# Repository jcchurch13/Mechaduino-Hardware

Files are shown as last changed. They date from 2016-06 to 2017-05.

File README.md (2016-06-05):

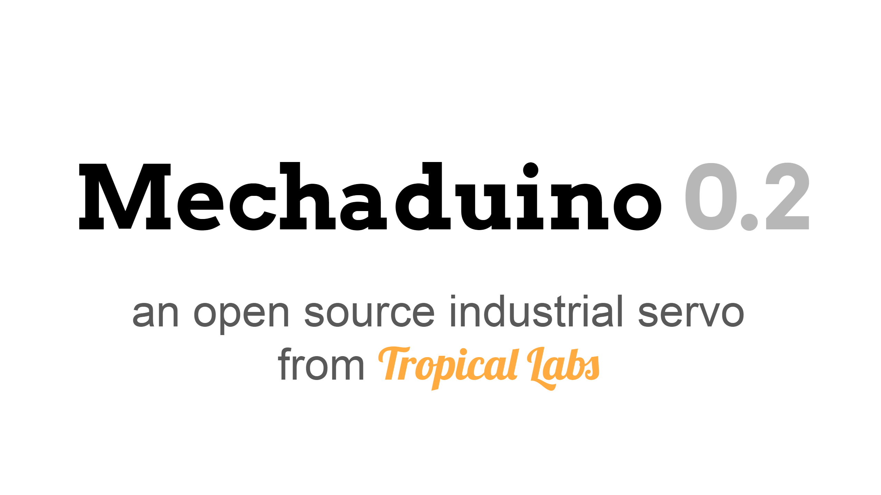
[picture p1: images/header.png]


Engineers use servo motors to achieve the precision motion required in applications such as robotics, automation, and CNC manufacturing. Like RC servos, industrial servos actively correct for external disturbances. Unlike RC servos, industrial servos can provide very accurate motion, and often support advanced motion control modes. Unfortunately the cost of industrial servos is prohibitive to the individual maker (thousands of dollars per motor).

We've been developing an affordable open-source industrial servo motor, opening the door to sophisticated mechatronics applications. Our design leverages the low cost of mass produced stepper motors. We are able to achieve very high resolution via 14b encoder feedback (after calibration routine!).



## Project Goals

 - Position, velocity, torque loops
 - Step & direction inputs for drop-in compatibility with stepper motors / step stick
 - I2c, serial inputs
 - Customizable/open source with access to internal variables
 - Transparent and user-definable control algorithms (commercial servos often lack this)
 - Arduino compatible with easy to use interface
 - High resolution pointing (sub 0.1 degree)
 - Low cost (should not be a huge leap from stepper + stepstick cost)
 - Serial interfaces for inter-motor communication
 - On-board processor allows for stand alone for simple applications
 - Adjustable commutation profiles
 - PID auto tuning
 - Anti-cogging capable
 - Open to customization. Outside of our firmware, we see Mechaduino as a very useful hardware package. If you would like to use the stepper motor in open loop mode w/ encoder to verify location, you can do that.

## Strategy

An industrial servo motor can be broken down into four main components (below). First we looked at each of these components and tried to piece together an affordable breadboard-level prototype. After some experimentation, we were able to distill out a working lineup of components. From there, we've been iterating on our design, working out all the kinks, and tuning the control loops. It's starting to come together!

...Back to those four main components:

1. The actual motor, usually of the brushless dc variety. When you look at industrial servo motors, a big chunk of the cost is the motor itself. They are often custom built, or at least built in limited quantities, which means $$$. Watt for watt, I'd guess that a mass produced NEMA 17 or NEMA 23 stepper motor is between a tenth and a hundredth the cost of the BDC motors used in industrial servos. Although their design is optimized for "stepping," stepper motors are really just 50-pole brushless dc motors. They can be controlled exactly like a more traditional 3 phase BDC motor with more poles. So that's the plan. It's working!

2. A sensor for feedback, usually an encoder. Optical encoders are pretty standard, but get quite pricey if you want high resolution and/or absolute position information. We were intrigued by some of the cheap, high resolution magnetic encoders offered by vendors like AMS. It turns out that although they claim 12 and 14 bit resolutions (that's 0.09 and 0.02 degrees respectively), they suffer from non-linearities on the order of a degree or so! However, we found that this non-linearity is very repeatable, and we were able to develop a quick, self contained (on motor) calibration routine that restores resolution to better than 0.1 degrees. (More on this later. This was a significant design effort and is worthy of its own build log!)

3. Drive circuitry/power electronics to excite the motor windings. Many industrial servos use discrete H bridges. Each phase requires it's own H bridge ( for a two phase motor... half bridges for each in a three phase motor), which consists of at least 4 if not 8 (...including freewheeling diodes) discrete switching devices. Throw in gate drive circuitry, and things start to get expensive. We hoped to find a single-chip, integrated solution that would allow for current feedback, and we found just that in the A4954 dual full bridge PWM driver.

4. Control Electronics. Usually a microcontroller or FPGA. Early on, we decided that Arduino compatibility was a must in order to make the firmware as accessible as possible. We chose to use a SAMD21 ARM M0+ (Arduino Zero compatible) processor to balance cost and performance. Our breadboard prototype system verified that this processor was more than capable of executing the necessary algorithms.

### Application Examples:

 - [Fine, closed loop positioning for 3D printers](https://www.youtube.com/watch?v=T1HIWAiMrfY)
 - Fine pointing for optics (laser, telescope, camera gimbal)
 - Velocity loop for a record player
 - Force feedback/impedance control for robotics
 - Force feedback for gaming controllers
 - Adjustable mechanical impedance: virtual spring,mass,damper
 - Electrical gearing between two axes on a cnc machine, etc.
 - Haptics
 - Tele-operation
 - Gravity-cancellation (counter the gravitational torques on a robotic arm for example)
 - Load detection and characterization (simple case: use as a scale!)
 - Paper towel/tp dispenser
 - Variable load (brake)
 - Variable load (generator)
 - After market valve control (automate a garden hose, etc)

### Other Advantages:

- Finer resolution than stepper motors (0.02 degrees)
- True closed loop for disturbance rejection
- Lower power consumption: only uses power to fight disturbances. This in turn means higher peak torque.
- Absolute position control (not incremental). No need to home on power-on.

## License

All Mechaduino related materials are released under the
[Creative Commons Attribution Share-Alike 4.0 License](https://creativecommons.org/licenses/by-sa/4.0/)

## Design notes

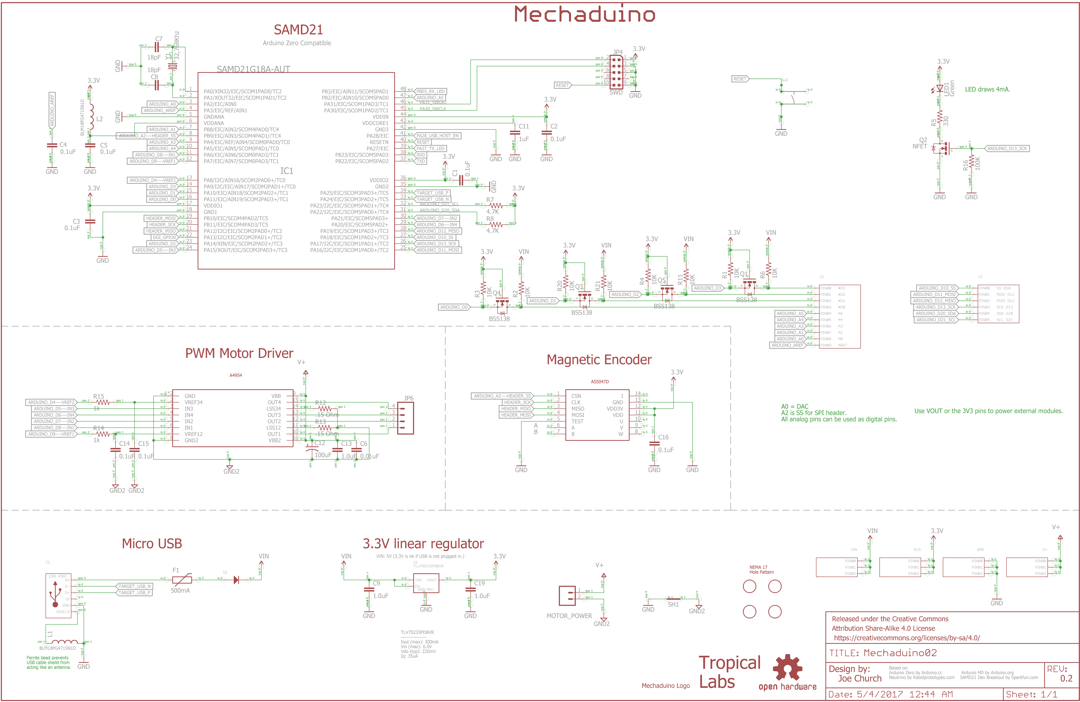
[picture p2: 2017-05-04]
Mechaduino_02_Schematic.png

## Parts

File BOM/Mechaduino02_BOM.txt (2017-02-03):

Partlist exported from C:/Users/jcchurch/Documents/GitHub/Mechaduino-Hardware/Mechaduino02.sch at 2/3/2017 1:24 PM

Qty Value                     Device                                 Package                       Parts                             Description                                                                         
1                             DIODE_SOD-123                          SOD-123                       D1                                Library:  MF_Discrete_Semiconductor                                                 
4                             HEADER_01X03_PTH_2.54MM                PTH_2.54MM_01X03              3V3, GND, V+, VIN                 Library:  MF_Connectors                                                             
1                             HEADER_01X06_PTH_2.54MM                PTH_2.54MM_01X06              J3                                Library:  MF_Connectors                                                             
1                             HEADER_01X10_PTH_2.54MM                PTH_2.54MM_01X10              J2                                Library:  MF_Connectors                                                             
1                             M025MM                                 SCREWTERMINAL-5MM-2           MOTOR_POWER                       Standard 2-pin 0.1" header. Use with                                                
1                             M04PTH                                 1X04                          JP6                               Header 4                                                                            
1                             TACT_4.2MM                             TACT4.2MM                     SW2                               Library:  MF_Switches                                                               
1                             USB_MICRO_RIGHT                        MICROUSB-RIGHT                J1                                Library:  MF_Connectors                                                             
2   .15 Ohm                   R-US_R1206                             R1206                         R12, R13                          RESISTOR, American symbol                                                           
1   0.01uF                    CAP0402                                0402-CAP                      C6                                Capacitor                                                                           
8   0.1uF                     CAP0402                                0402-CAP                      C1, C2, C3, C4, C5, C14, C15, C16 Capacitor                                                                           
2   1.0uF                     CAP0402                                0402-CAP                      C9, C19                           Capacitor                                                                           
1   1.0uF                     CAP0603                                0603-CAP                      C13                               Capacitor                                                                           
1   100K                      R-US_R0402-VISHAY                      R0402-VISHAY                  R16                               RESISTOR, American symbol                                                           
1   100uF                     CAP_POLD                               PANASONIC_D                   C12                               Capacitor Polarized                                                                 
8   10K                       R-US_R0402-VISHAY                      R0402-VISHAY                  R1, R2, R3, R4, R6, R11, R20, R21 RESISTOR, American symbol                                                           
2   18pF                      CAP0402                                0402-CAP                      C7, C8                            Capacitor                                                                           
2   1k                        R-US_R0402-VISHAY                      R0402-VISHAY                  R14, R15                          RESISTOR, American symbol                                                           
1   1uF                       CAP0402                                0402-CAP                      C11                               Capacitor                                                                           
1   32,768Khz                 CRYSTAL2012                            CRYSTAL-SMD-2.0X1.2           Y1                                Various standard crystals. Proven footprints. Spark Fun Electronics SKU : COM-00534 
1   330                       R-US_R0402-VISHAY                      R0402-VISHAY                  R5                                RESISTOR, American symbol                                                           
2   4.7K                      R-US_R0402-VISHAY                      R0402-VISHAY                  R7, R8                            RESISTOR, American symbol                                                           
1   500mA                     PTCSMD                                 PTC-1206                      F1                                Resettable Fuse PTC                                                                 
1   AS5047D                   AS5047D                                TSSOP14                       U$4                                                                                                                   
1   AVAGO_DRIVERTHERM         AVAGO_DRIVERTHERM                      TSSOP16_THERM                 U$1                                                                                                                   
2   BLM18PG471SN1D            INDUCTOR0603-TDK                       0603-TDK                      L1, L2                            Inductors                                                                           
4   BSS138                    MOSFET-NCHANNELSMD                     SOT23-3                       Q1, Q3, Q4, Q5                                                                                                        
1   FRAME-LEDGER              FRAME-LEDGER                           CREATIVE_COMMONS              FRAME1                            Schematic Frame                                                                     
1   Green                     0044_KPT-2012YC                        CHIPLED_0805                  LED1                              LED YELLOW - SMD - 0805                                                             
1   MECHADUINO_LOGO           MECHADUINO_LOGO                        MECHADUINO_LOGO               U$5                                                                                                                   
1   NEMA17_HOLE_PATTERNNEW    NEMA17_HOLE_PATTERNNEW                 NEMA17_HOLE_PATTERN_2         U$2                                                                                                                   
1   NFET                      MOSFET-NCHANNEL2N7002PW                SOT323                        Q2                                Common NMOSFET Parts                                                                
1   OSHW-LOGOMOD              OSHW-LOGOMOD                           OSHW_LOGO_COPPER_MOD          LOGO4                             Open Source Hardware Logo                                                           
1   SAMD21G18A-AUT            INTEGRATEDCIRCUITS_1792_SAMD21G18A-AUT INTEGRATEDCIRCUITS_TQFP48-7X7 IC1                               Atmel D21 32bit ARM Cortex-M0  microcontroller - 48 PIN TQFP                        
1   SHORT-HA5                 SHORT-HA5                              SHORT_ALL-50                  SH1                               Short between two nets                                                              
1   SWD                       CONNETTORI_0171_PH127-205DF055G00A     CONNETTORI_PINHEAD-2X5-P127   JP4                               2x5 PASSO 1,27                                                                      
1   TLV70233PDBVR             TLV70233PDBVR                          SOT-23-5                      U1                                Manufacturer Part #: TLV702                                                         
1   TROPICAL_LABS_LOGO_1LOGO3 TROPICAL_LABS_LOGO_1LOGO3              LOGO3                         U$3

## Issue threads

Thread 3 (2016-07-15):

Vector control

markfinn, 2016-07-15:
From what I can understand of the firmware, and from looking at the schematic, you are missing out on field / vector control of the motor.  With vector control you control the torquing current and the "magnetizing current" (think of the current that is 90 degrees out of phase with the torquing current).  This allows for a few things:

- Easy "current advance" and it's more general cousin "field weakening" which is advance past the point needed for just overcoming inductance.  It allows a much higher top speed when torque is allowed to decline.
- Better position accuracy (and lower position latency) by combining the encoder with the driving currents and a motor model through a Kalman filter.  This especially would help here with the 50 pole motor.
- Some amount of force feedback
- Quieter and cooler operation through sine-drive commutation over square wave. I can't tell exactly what you have implemented now from a quick look at the firmware, so this one might not count.

The reason I bring this up in the hardware project is that you are missing motor feedback that is needed to allow this.  The "normal" way to do vector control is to control the phase drive voltages (via PWM) and sense the phase currents.  To do that you would need to add an amplifier to bias and scale the current sense resistors, and ADCs (maybe in the MCU already? I didn't look) that can sample at least around 40 per pole, or 2000 times per rotation on a 1.8 degree stepper.

Another option that may be possible (I'm making this one up as I go along, I don't know if it's been done before or disproven)... Since you are using a bridge driver that self-regulates current, I think it might be possible to implement vector control using a "control the current, read the phase voltage via PWM transitions" model.  This would depend on being able to change the current Vref values at at least a few times per pole to control the phase current directly, and having some digital feedback from the motor phase outputs to know when the A4954 switches between internal PWM modes.  This method would only need a diode or two and some resistors for each of the 4 motor leads.  The big sticking point would be whether the A4954 Vref input has that kind of frequency response.  I don't see anything to give a hint in the datasheet, so it might have to be determined by experiment.

Either of these methods would allow estimating the back-emf of the motor, which gives an estimate of motor position, and when combined with knowing the phase voltage or current give force feedback and the ability to directly control the 2 current vectors occurring in the motor.

Looking forward to getting some hardware...  I'm glad someone is finally doing this!

jcchurch13, 2016-07-15:
Hi Mark,
We actually are using a form of vector control.  We sinousoidally vary the vref inputs to the a4954 driver as you describe.  Frequency response does not seem to be an issue based on performance.
-Joe

markfinn, 2016-07-15:
I went through the code enough to understand it now. I should have been more specific about using "vector" vs "field oriented" above.  It's been a while since I've looked at this stuff and I got a little sloppy.

What you're doing is vector based, but you're not really getting field control yet because even though you try to command Iq (torque current) via output() and implicitly command Id to zero, the external controller (The PWM current control loop in the A4954) can't magically make those currents happen in the face of inductance and motor irregularity.  The real Iq ends up lagged and not matching the commanded one, and the real Id ends up nonzero.

I see you've tried "phase advance."  Was that by using a motor model (backemf, resistance, inductance, position) to try to estimate the the actual phase currents and Iq, Id?   If that works well enough, maybe my request for real feedback isn't needed.  I just haven't seen any examples where current sensing was modeled instead of measured before so I assumed it didn't work well.

Sorry if you've thought about all this already, I'm a little excited about the project.  For the record, my looking into this part came from seeing the FAQ about motor speed only being easy up to 300rpm on the nema17, combined with the link you posted to the 1.8A nema 23 stepper.  It has an inductance of 17mH, so I started getting a bit worried about top speed even at 40 volts.

jcchurch13, 2016-07-16:
Hi Mark,

You are correct:  We are using vector control, but not field oriented control.  There are a lot of advantages that come with field oriented control, but we've found that it would drive the hardware cost and complexity up quite a lot.  By off-loading the current loop to the A4954, we've found that we can deliver pretty impressive performance at an accessible hardware cost.
Thanks for your input!
-Joe

markfinn, 2016-07-16:
I'm not saying don't use the A4954, I'm saying sense the current.  You
could maybe do it well enough with just AC coupling the shunt into the ADC
channels on the MCU.  That would only be 2 extra caps and 4 resistors.

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

dzid26, 2020-07-23:
I am just going to link to a discussion where I am coming to the same realization as @markfinn regarding a lack of current sensing and FOC implications.
https://groups.google.com/g/smart-stepper/c/LuQkAaiCvPs/m/Nzos9Bh_CAAJ

I am too wondering if it would work to implement a modified (even simpler) open-loop FOC where currents are not sensed but assumed to be correct based on the commanded currents.
I am thinking that without reading or estimating the real current the method wouldn't be perfect but perhaps a little improvement could be noticeable. At very least the math for field weakening, etc could be reused instead of guessing offsets between phases to weaken the field.
Additionally, it seems sensor latency is already a limiting factor for higher speed, so it would need to be accounted for separately via phase-advancement trick.

Closed 2016-08-22.

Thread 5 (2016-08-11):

Current BOM lists 10uF 0402, board uses 10uF 0805 for C18, C10

thantik, 2016-08-11:
Found this mistake while reflowing my boards; caused me to get a digikey order slightly wrong.

jcchurch13, 2016-08-11:
Fixed, thanks!

Closed 2016-08-11.

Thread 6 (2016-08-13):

BOM mismatch between Value and Device - IC2 3.3V regulator - line 31

bitbangr, 2016-08-13:
BOM Line 31 shows 3.3V regulator AP2112K-3.3 as the value however the specified device is AP2202-ADJ.

The AP2202-ADJ needs additional circuitry on pin 4 to set the correct output voltage.

Perhaps update the BOM to reflect the correct device?

1   AP2112K-3.3               AP2202-ADJ                             SOT23-5@1                     IC2

jcchurch13, 2016-08-14:
Fixed, thank you!
-Joe

Closed 2016-08-14.

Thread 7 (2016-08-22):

R6, should this be a 10k?

thantik, 2016-08-22:
There are multiple places that I'm seeing a 10k pullup on the RESET line:

https://cdn.sparkfun.com/datasheets/Dev/Arduino/Boards/sparkfun-samd21-mini-breakout-v10.pdf

http://www.atmel.com/Images/Atmel-42181-SAM-D21_Datasheet.pdf -- Page 1022 under 39.4. External Reset Circuit

But on the schematic and board, R6 is listed as a 330ohm.  This is a pretty strong pullup, is there a reason for the deviation?

jcchurch13, 2016-08-22:
Hi!  R6 is used as a current limiting resistor here (similar to the second resistor in the 39.4 example above).  R1 acts as the pullup (100k).

Closed 2016-08-22.

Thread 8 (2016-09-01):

AS5047D Magnetic Encoder Power Management issue.

bitbangr, 2016-09-01:
I was checking over the [Datasheet for the AS5047D Magnetic Rotary Position Encoder](http%3A%2F%2Fams.com%2Feng%2Fcontent%2Fdownload%2F595083%2F1609657%2F320155&sa=D&sntz=1&usg=AFQjCNHJLUOwhbDV-abh1qcGxdTLYPkByQ)

The section on power management has two configurations. One for 5V operation and the other for 3.3V operation.

For 3.3V operation it states -> "In 3.3V operation, VDD and VREG must be tied together."

In Figure 10 the "3.3 Operation" diagram shows VDD and VDD3V3 tied together with one 100nF cap to ground.

It would seem to me that C17 1uF should be removed from this circuit and pins 11 and 12 of the AS5047D should be tied together.

This could easily be fixed on the current board by a small bridge between C16 and C17 on the top of the board after removing C17.

PS I also [reported this to the Mechaduino Google Group](https://groups.google.com/forum/#!topic/mechaduino/e2BsRLsDtlw)

jcchurch13, 2016-09-01:
We are aware of this discrepancy but have found that it does not seem to have any noticeable effect on performance.  We will make the change in the next rev.
Thanks!
-Joe

bitbangr, 2016-09-01:
Cool.  I'll close this then.

Closed 2016-09-01.

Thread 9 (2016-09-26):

Opensource.com article

spotrh, 2016-09-26:
Joe,

Apologies for opening a github issue, but I couldn't find an email address for you. I'm writing an article for opensource.com on some of the best open source hardware innovations in 3d printing in 2016, and I want to feature the Mechaduino. Would you be able to point me to a picture of the Mechaduino (maybe the "banana" picture from the kickstarter page) that I could use under a Creative Commons license (CC-BY-SA would be ideal)?

Thanks in advance,

Tom Callaway <tcallawa@redhat.com>

jcchurch13, 2016-09-26:
Feel free to use any of the photos on our hackaday.io page:

https://hackaday.io/project/11224-mechaduino

All Mechaduino related materials are released under the Creative Commons Attribution Share-Alike 4.0 License!

Closed 2016-09-26.

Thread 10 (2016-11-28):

Feature request : Gadgeteer port

arthurwolf, 2016-11-28:
Hey.

As part of the Smoothieboard v2 hardware design, we are planning a very complete series of "extension boards" : goo.gl/XP5iZc
Those boards will all use the "Gadgeteer" socket. It is small, it's a very nice and well designed standards, a lot of boars already exist for it. We also hope to encourage other Open-Source controller board designers ( running Smoothie or otherwise ) to also use these in their hardware.
If you were to add a Gadgeteer port to your board, that'd make it super easy to interface will all of the Smoothieboard v2 hardware boards ( and possibly other boards in the future ).
What do you think ? Maybe for a v2 of your hardware ...

Cheers.

npgoalkeeper, 2018-07-26:
RIP Smoothieboard

arthurwolf, 2018-07-26:
What ? Why ?

On Thu, Jul 26, 2018 at 2:46 AM npgoalkeeper <notifications@github.com>
wrote:

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

--
Courage et bonne humeur.

DirtyEngineer, 2018-07-26:
Because development seems to have come to a full stand still?

I think this comment stems from this thread. https://github.com/jcchurch13/Mechaduino-Hardware/issues/14#issuecomment-407940180

arthurwolf, 2018-07-26:
Eh thanks, answered there. This is most definitely wrong.

On Thu, Jul 26, 2018 at 2:51 PM Jon Raymond <notifications@github.com>
wrote:

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

--
Courage et bonne humeur.

npgoalkeeper, 2018-07-26:
Yea I thought it was dead as the website said the release would be in 2017, and the files haven't been updated in awhile. I like the the thing you're developing with F360 and smoothieware, though.

arthurwolf, 2018-07-27:
It's late, but that's to be expected for such a huge project :)

On Thu, Jul 26, 2018 at 11:51 PM npgoalkeeper <notifications@github.com>
wrote:

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

--
Courage et bonne humeur.

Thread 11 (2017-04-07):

Compilation error w/ Arduino 1.8.2 IDE

eudoxos, 2017-04-07:
After opening the firmware in Arduino, verification fails with error from gcc. I tried to google things up, nothing shows up. Maybe some problem between keyboard and chair. I am new to mechaduino so maybe I am missing something obvious. I looks as if types were not recognized, but there is no error about #include not being found. These are the first few messages. Thanks for help!

```
sketch/analogFastWrite.c: In function 'syncADC':
analogFastWrite.c:17: error: invalid type argument of '->' (have 'uint16_t')
   while (ADC->STATUS.bit.SYNCBUSY == 1)
             ^
sketch/analogFastWrite.c: In function 'syncDAC':
analogFastWrite.c:24: error: 'DAC' undeclared (first use in this function)
   while (DAC->STATUS.bit.SYNCBUSY == 1)
          ^
sketch/analogFastWrite.c:24:10: note: each undeclared identifier is reported only once for each function it appears in
sketch/analogFastWrite.c: At top level:
analogFastWrite.c:29: error: unknown type name 'Tc'
 static __inline__ void syncTC_8(Tc* TCx) __attribute__((always_inline, unused));
                                 ^
analogFastWrite.c:30: error: unknown type name 'Tc'
 static void syncTC_8(Tc* TCx) {
```

mikbeng, 2017-10-11:
I have the same problem here, did you find any solution to this?

jcchurch13, 2017-10-11:
I would double check that you have the correct board selected in the Arduino IDE (Arduino/Genuino Zero, (Native USB port)).  I've seen similar issues when I've forgotten to select the right board.

-Joe

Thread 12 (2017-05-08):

NEMA 34 and larger?

linuxras, 2017-05-08:
What would be required to make this work with larger stepper motors like NEMA 34 etc.?

tknapstad, 2017-05-09:
Mainly a beefier motor driver which will probably alter both the schematic and layout, as well as an adapter plate for the nema34 footprint

npgoalkeeper, 2018-08-23:
Just a bracket. Theres a high power version of this for nema 34's.

DirtyEngineer, 2018-08-23:
I might mention there's a Kickstarter for a similar product right now. https://www.kickstarter.com/projects/301805155/ustepper-s-line

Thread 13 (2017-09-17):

Flyback diodes

Blaster1920, 2017-09-17:
Hi,
Why don't you add these diodes [https://github.com/watterott/SilentStepStick/blob/master/hardware/StepStick-Protector_v11.jpg](url) directly on your board? I think it would help a lot the printing quality.

npgoalkeeper, 2018-07-24:
Like in a TL-Smoother Configuration?

Blaster1920, 2018-07-24:
Yes.

npgoalkeeper, 2018-07-24:
Why not just solder one between the stepper and the mechaduino motor.

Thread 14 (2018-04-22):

Feature request: Trinamic drivers

udidnazime, 2018-04-22:
Any word of advice on interfacing trinamic drivers on board instead of the a4954 stepper drivers? This so stepper operation can be quieter.

julidau, 2018-07-23:
could you elaborate further on that thought? Are there any trinamic products specifically that you could suggest ?

npgoalkeeper, 2018-07-24:
I really like the look of the TMC4362A-LA, and they also happen to be cheaper at Digi-key than the TMC4330A-LA, and its information can be found here: https://www.trinamic.com/products/integrated-circuits/details/tmc4361a-la/ as well as the pinout.

julidau, 2018-07-24:
These are nice motion controllers.

They can talk to the AMS5047 directly and implement closed loop stepper control using the encoder feedback.

**But** they do not contain a driver stage or a stepper driver (current controller). So while they are a nice replacement for the M0+ core (the Atmel SAMD21) on the Mechaduino, they cannot replace the A4954.

I feel that i should also mention the [PanDrive stepper controllers from Trinamic](https://www.digikey.de/product-detail/de/trinamic-motion-control-gmbh/PD42-2-1140-TMCL/1460-1100-ND/5013387) that are using a similar chip to implement something close to the Mechaduino. While the linked one is quite pricey i think they are a better option then changing the mechaduino hardware.

npgoalkeeper, 2018-07-24:
Would it be possible to use that with the tmc 262 as the stepper driver? or would that drive the price of this device to be over a hundred dollars (im trying to add this to my prusa i3 mks MMU kit. I’ve looked at Trinamic’s PANdrive systems and am not interested to to the insane price).

npgoalkeeper, 2018-07-24:
In that case, what about using a TMC5160-TA? I wasn’t able to find it beforehand on the other comment, however it includes the features of the TMC2660 with an input for an encoder, along with the features of the TMC4362A-LA. along with that, it is chainable via UART on the datasheet. Along with that, you can add extrernal mosfets, making this closed loop stepper sytem seem more attractive to cnc applications. e. g. one large stepper board chained to multiple smaller, cheaper ones. This IC is also cheapper than the TMC262 and TMC4362-LA at digikey.

julidau, 2018-07-25:
well that chip sure looks great. I really wish i would have known about it before making a driver based on the TMC2660 :)

That chip only has a few drawback though:
- The Encoder interface accepts quadrature encoders only. It makes sense (most stepper motors come with quadrature encoders either build in or added) but is different from the TMC4362-LA, which also accepts absolute position encoder feedback. Not that one would need that anyway, quadrature should be fine for most applications. A replacement for the AMS5047 would be the [AMS5601](https://www.digikey.com/short/j5v2mn) with a quadrature interface.
- The external mosfets are not optional, they are required. The chip only contains mosfet drivers. This is not that big of a deal as low power mosfets can be had for a buck each, but one will need 8 of them.

I am quite confident that, using the TMC5160-TA, a drop-in replacement for the mechaduino can be made. I'm not sure about doing it on two layers, but it might be possible. I unfortunately lack the time to do so :(

npgoalkeeper, 2018-07-25:
Huh. So to get a better, cheaper motion controller/ driver, you have to sacrifice some precision? Not like over 10 thousand positions would affect something that only steps to 400. When will the TMC 2660 variant of this driver be available? Will it still maintain the SAMD21G18A-AUT? No Rush.

julidau, 2018-07-25:
just in case it seemed that way: i am not affiliated with the mechaduino project :wink:.  I just happen to own one...

As it seems this project died over a year ago, i don't think there will be any version using a trinamic driver. I was working on a different driver style using the TMC2660 (one in a format similar to [this one](https://www.aliexpress.com/item/Dawupine-Schrittmotorsteuerung-Leadshine-DM856-2-phasen-schrittmotor-57-86-Digitale-Schrittmotortreiber-20-80-Vdc-1A-bis/32835988065.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,searchweb201603_46,ppcSwitch_2&algo_expid=c5cd6080-6b93-4cec-9fca-baf0c47b8db8-6&algo_pvid=c5cd6080-6b93-4cec-9fca-baf0c47b8db8&priceBeautifyAB=0)).

Regarding the encoder and the loss of precision: The AMS5047 is currently hard to come by (mouser has a few left i think) and the one i proposed was the "next best thing". Whether that would be the optimal choice i cannot say for certain. AMS might have 14bit encoders with a quadrature interface in their lineup. I was not looking super hard to be honest…

Cheers :)

npgoalkeeper, 2018-07-26:
Wow. Now I feel stupid. So um, thanks for your help. It seemed like you were putting an awful lot of effort into your replies, and I thank you for that. It seems that a lot of things 3D-Printing as far as electronics go have died in the past year. The Smoothie-V2 seems to be dead, as well as many other awesome boards. With duet being at the, top they really have no reason to innovate and the revolve board will be way too expensive for a standard user. This makes me curious of someones gonna end up making a REALLY successful kick-starter that includes 3D printing electronics. Anyways, thanks again, and one last thing: Are you gonna make that motor driver design public on easyEDA? I think they guys over at reprap would have a field day over that.

julidau, 2018-07-26:
No worries! I just wanted to lower the expectations a bit :)

Yes, i was planning on making the design publicly available after fully testing it out. And who knows? Maybe i will come around to making a driver board thats screws to the back of the stepper like mechaduino does. I too am curious what the future holds...

npgoalkeeper, 2018-07-26:
I just did some reading and found out that the TMC5130 has the same features as the 5160, however it has internal MOSFETS, so you may want to check that out at a later date.

arthurwolf, 2018-07-26:
@npgoalkeeper  Smoothie v2 is most definitely not dead, both Smoothie v1 and v2 are very actively developed, it's just we are doing extremely ambitious things at the moment so there are longer development time spans than usual.  I've just sent the gerber for the first proto of v2 to the board house, and we already have protos for v2-mini and v2-pro. And v2 firmware can laser cut and cnc mill at this point.

npgoalkeeper, 2018-07-26:
Sooo its just issues with FW and getting the pcb's manufactured at this point?

arthurwolf, 2018-07-27:
Mostly yes.

On Thu, Jul 26, 2018 at 11:53 PM npgoalkeeper <notifications@github.com>
wrote:

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

--
Courage et bonne humeur.

npgoalkeeper, 2018-07-28:
So I found the AMS AS5311 magnetic hall effect IC, and it uses an ABI interface (looks like it can be programmed to ABN for the TMC5130) and all it requires is an SDI/SCL interface to program. I’m going to try and make something close the mechaduino, and it should in theory only need a location to get to.

julidau, 2018-08-22:
hey,
how is your project coming along ?
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
npgoalkeeper, 2018-09-07:
"Integrated Drive" IC's have too low of an amperage rating for CNC applications. On second thought, I will copy the TMC5160 reference design. Updates on the project will be posted here: https://github.com/npgoalkeeper/Closed-loop-stepper/blob/master/README.md
(I really need a name for it)

npgoalkeeper, 2018-09-14:
Just a bit of an update, I've been talking with trinamic and they have convinced me to simply use a tmc2130, with it the tmc2160 coming out soon.

npgoalkeeper, 2018-09-15:
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
Its begun.

npgoalkeeper, 2018-09-17:
So I did a small amount of research on the VHF ringingyou spoke of, and found a thing called a snubber network. Are therea any downsides to using an RCD snubber? It seems to do the same exact thing as the resistor, however it acts as more "active" filter that completely removes the inductance that causes this phenomenon. However, it seems like more than anything my main concern should be layout as far as efficiency goes when I make the tmc2160 version.

RGD2, 2018-09-18:
Yes, Snubber with diode is better - just more complex, more expensive, and
needs to be the right one.

 But yes, even just one resistor is acting as a snubber, just a simple
linear one.

Diode is non-linear, but so are ceramic caps not of np0 or c0g types — x7r
or any code other than the first two have capacitance which changes (quite
a lot!) with voltage — bad if you want a filter to stay tuned, but the
nonlinearity is actually good for avoiding resonance —   It is impossible
without that linearity. The whole point of a snubber is to prevent
unintended resonance and Q factor from causing a destructive over-voltage
condition.

The simple gate resistor is just enough to drop the Q of the RLC resonator
that exists because there is too little R in the gate pin, and the gate pin
+ pcb trace has some small inductance.

Then you can get into active circuits with transistors set to help turn off
the transistor faster by providing a lower impedance route to ground right
next to the main mosfet gate. All this becomes increasingly important as
you get up to the higher power levels / voltages and currents, since the
energy  in the ringing is a proportion of the gate drive power, and bigger
transistors mean much large gate capacitance, and require higher gate drive
current, and more careful handling of the snubbing.

On Mon, 17 Sep 2018 at 1:45 pm, npgoalkeeper <notifications@github.com>
wrote:

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
--
-- Remy

amoose136, 2018-09-22:
Just a note on the TMC2130-LA: my printer uses an Einsy Rambo 1.1a board as the driver and even though the RMS current is rated for 1.2A, in practice if you print with Marlin setting current at 800mA, the motors will reach a steady state temp around 50C. More current does not seem like a good thing here but I could see that maybe a longer Nema 17 could handle more and use more in milling applications with no issues.

npgoalkeeper, 2018-09-22:
Well I mean, this is mainly just for experinentation. Might be fun to use nema 17's in a milling machine just for wood or MDF or whatever.

npgoalkeeper, 2018-12-09:
So here's me a couple weeks later, after some testing. A friend and I have done some research and written the software, so we are going to make a motion controller that consists of A STM32F401 MCU paired with 2x TMC4361a's and 2x TMC2160's paired with 12a MOSFETs. As of right now, I do not want to share the link to access the project on EasyEDA

Psylenceo, 2019-04-19:
I keep screwing this up. Here is 2 boards I made up to allow more user functionality, use a TMC5130 or TMC2130, and eitehr a atmega32u4 or a atmega328PB. With a 3rd board in progress to offload the driver ic and instead have the user use a break out borad like the TMC2130-BOB, TMC5130-BOB, or TMC5160-BOB.

32u4 board - https://easyeda.com/kenm/Intele-step
328PB board - https://easyeda.com/kenm/mechaduino-328pb

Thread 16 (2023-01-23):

hardware serial rather than USB

jakobbak, 2023-01-23:
Hello All

Apologies for asking a question that may seem trivial, but I haven't been able to find an answer here or in the forks I was able to examine.

I was hoping to be able to use the serial interface, but over normal serial pins rather than USB. Are any of the existing pins available on the board attached to a serial peripheral? I realise I'll probably have to write up the serial handling myself, and happy to give that a shot, but in case there is another project that has done the same I'd be happy to take a pointer to such a project :)

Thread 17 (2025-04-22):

Missing Drill files

schnibbi, 2025-04-22:
For Ordering the PCBs at JLCPCP there is an issue with missing drill files.
Can you porovide the files ?

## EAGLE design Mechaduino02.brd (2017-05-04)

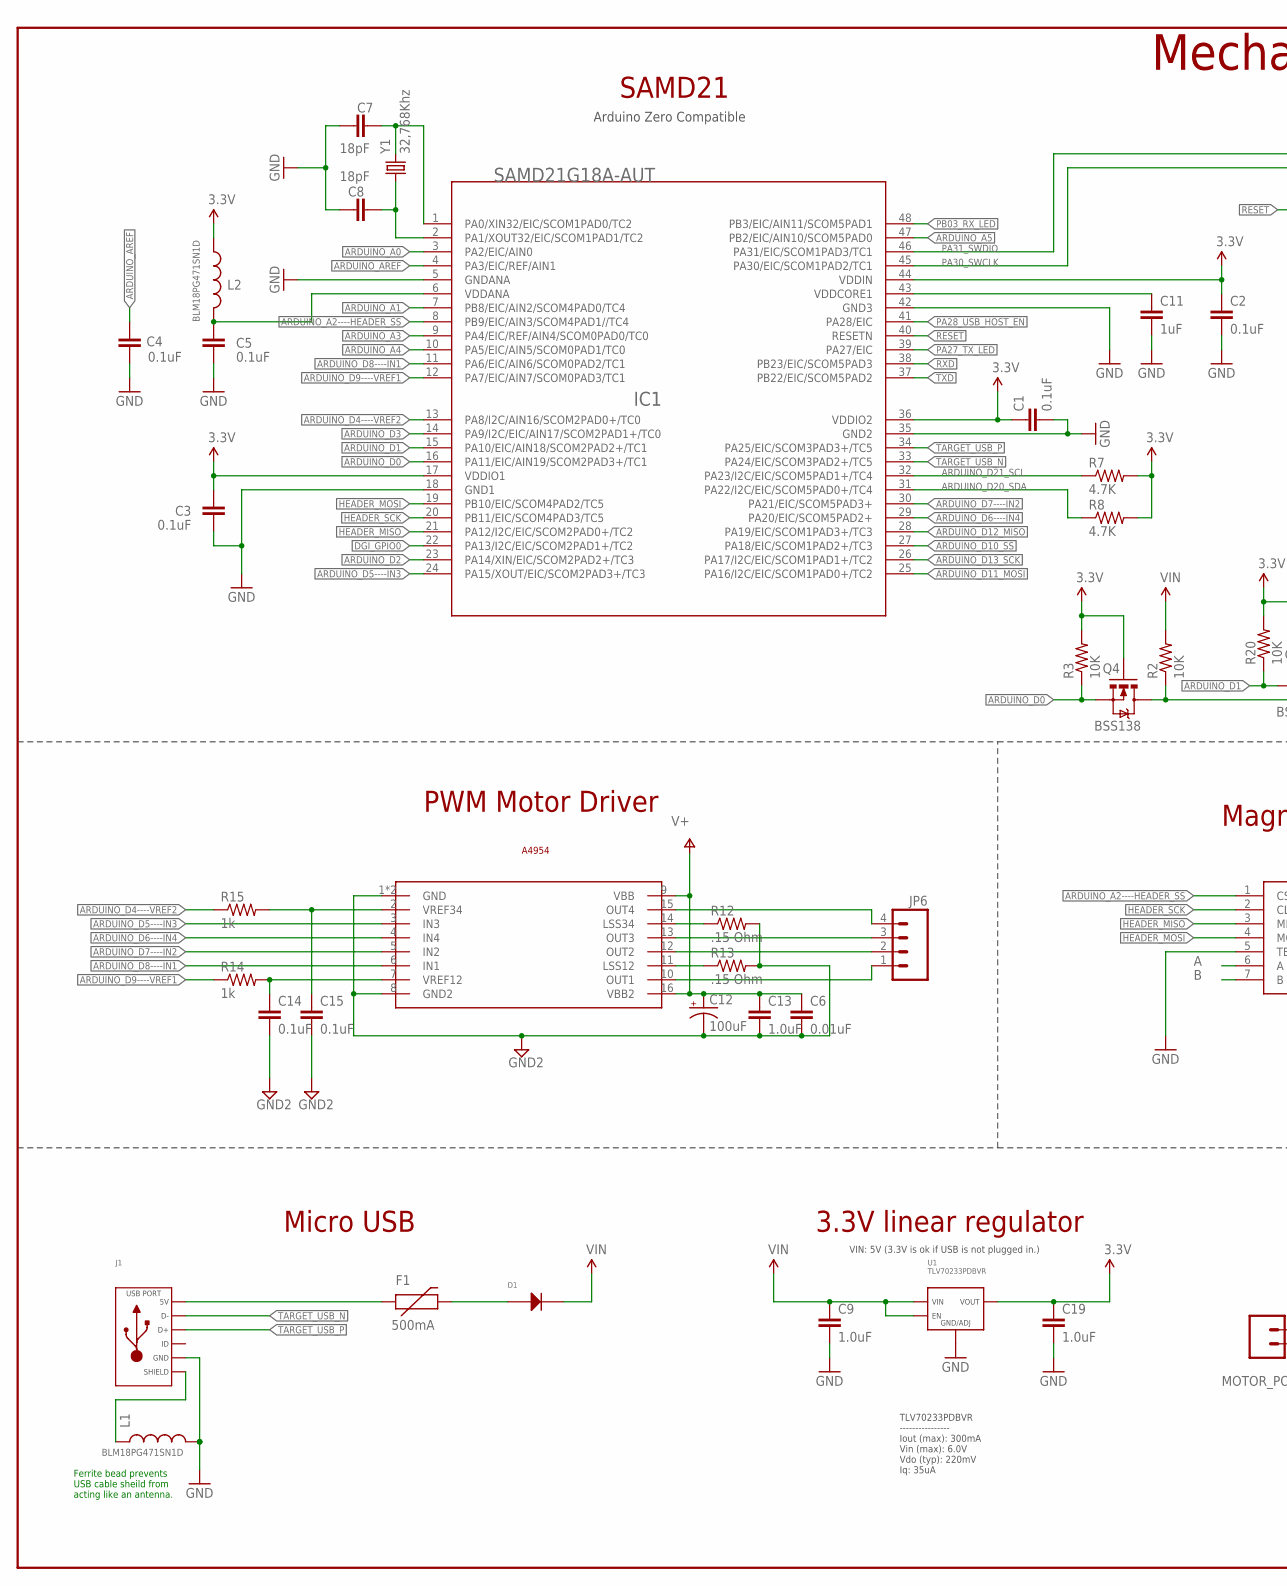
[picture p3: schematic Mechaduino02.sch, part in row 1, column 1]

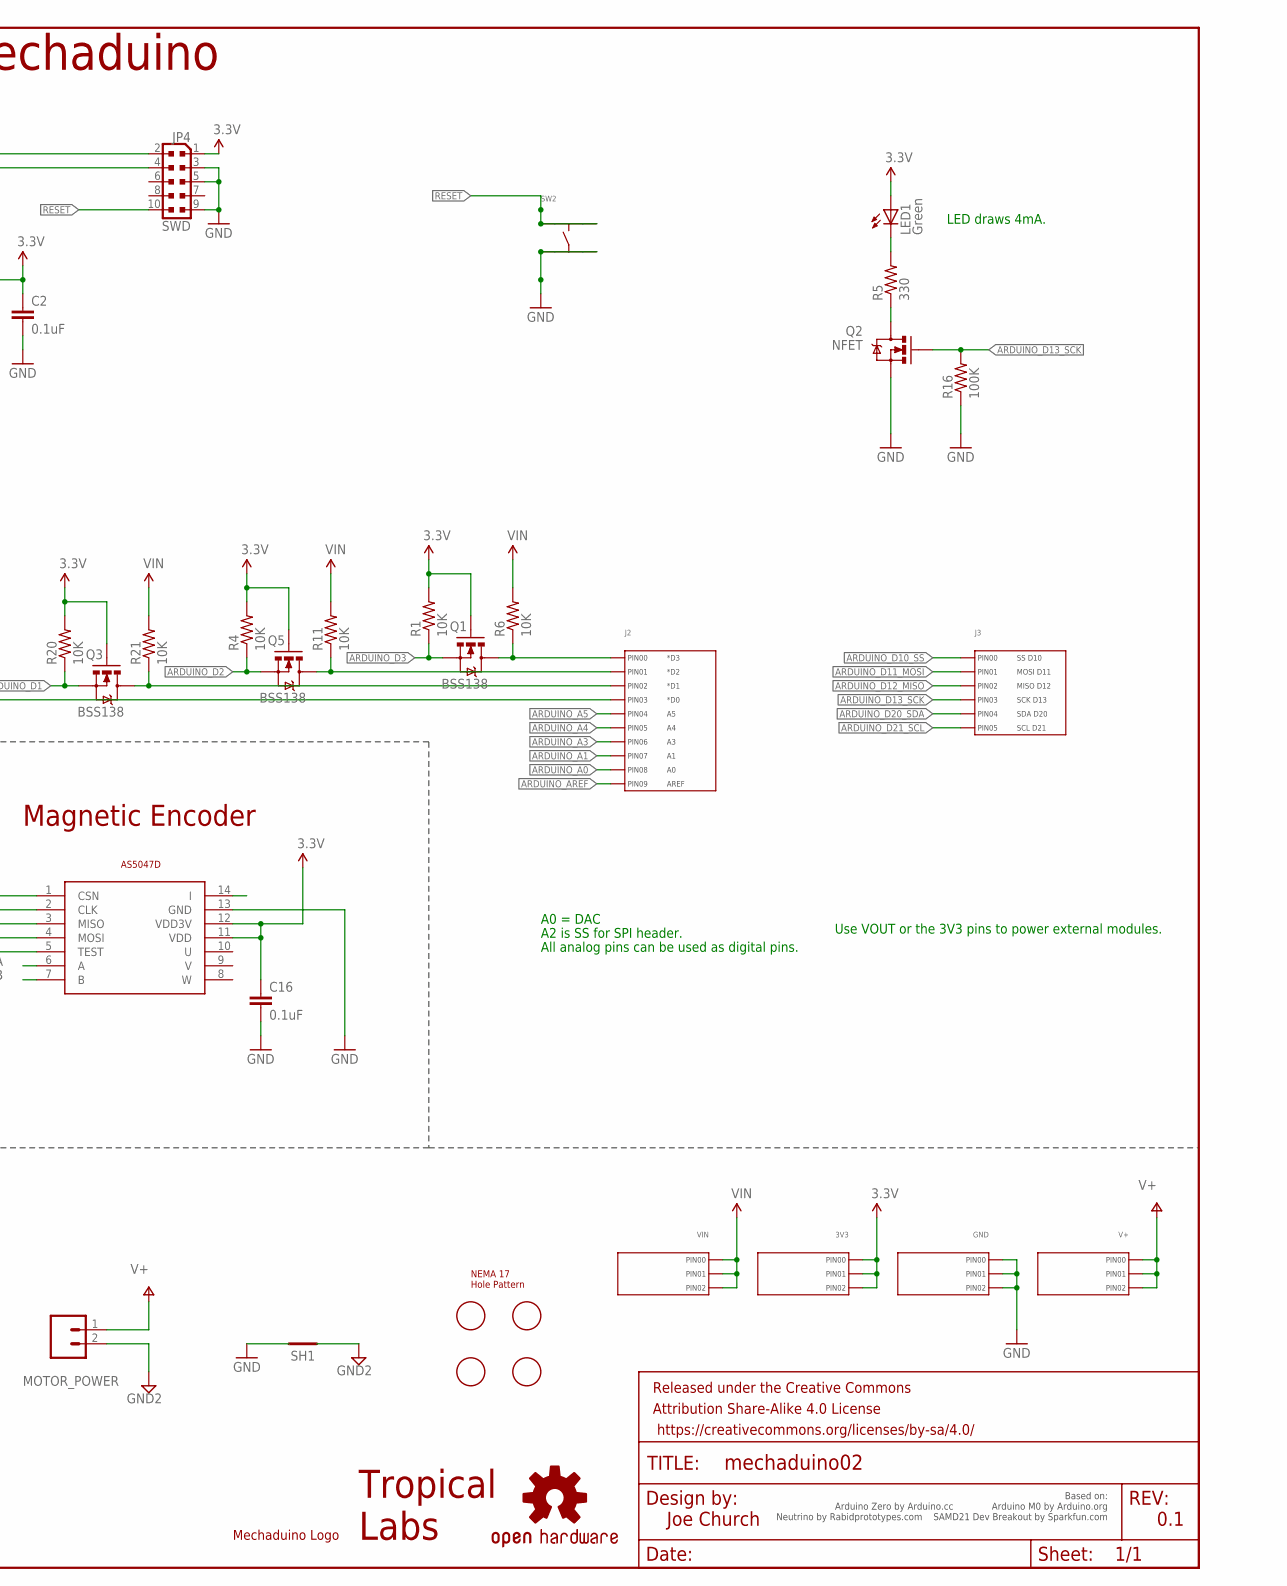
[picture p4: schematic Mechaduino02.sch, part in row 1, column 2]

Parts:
3V3: HEADER_01X03_PTH_2.54MM; PTH_2.54MM_01X03
C1, C2, C3, C4, C5, C14, C15, C16: 0.1uF; 0402-CAP
C6: 0.01uF; 0603-CAP
C7, C8: 18pF; 0603-CAP
C9, C19: 1.0uF; 0402-CAP
C11: 1uF; 0402-CAP
C12: 100uF; PANASONIC_D
C13: 1.0uF; 0603-CAP
D1: DIODE_SOD-123; SOD-123
F1: 500mA; PTC-1206
FRAME1: FRAME-LEDGER; CREATIVE_COMMONS
GND: HEADER_01X03_PTH_2.54MM; PTH_2.54MM_01X03
IC1: SAMD21G18A-AUT; INTEGRATEDCIRCUITS_TQFP48-7X7
J1: USB_MICRO_RIGHT; MICROUSB-RIGHT
J2: HEADER_01X10_PTH_2.54MM; PTH_2.54MM_01X10
J3: HEADER_01X06_PTH_2.54MM; PTH_2.54MM_01X06
JP4: SWD; CONNETTORI_PINHEAD-2X5-P127
JP6: M04PTH; 1X04
L1, L2: BLM18PG471SN1D; 0603-TDK
LED1: Green; CHIPLED_0805
LOGO4: OSHW-LOGOMOD; OSHW_LOGO_COPPER_MOD
MOTOR_POWER: M025MM; SCREWTERMINAL-5MM-2
Q1, Q3, Q4, Q5: BSS138; SOT23-3
Q2: NFET; SOT323
R1, R2, R3, R4, R6, R11, R20, R21: 10K; R0402-VISHAY
R5: 330; R0402-VISHAY
R7, R8: 4.7K; R0402-VISHAY
R12, R13: .15 Ohm; R1206
R14, R15: 1k; R0402-VISHAY
R16: 100K; R0402-VISHAY
SH1: SHORT-HA5; SHORT_ALL-50
SW2: TACT_4.2MM; TACT4.2MM
U1: TLV70233PDBVR; SOT-23-5
U$1: AVAGO_DRIVERTHERM; TSSOP16_THERM
U$2: NEMA17_HOLE_PATTERNNEW; NEMA17_HOLE_PATTERN_2
U$3: TROPICAL_LABS_LOGO_1LOGO3; LOGO3
U$4: AS5047D; TSSOP14
U$5: MECHADUINO_LOGO
V+: HEADER_01X03_PTH_2.54MM; PTH_2.54MM_01X03
VIN: HEADER_01X03_PTH_2.54MM; PTH_2.54MM_01X03
Y1: 32,768Khz; CRYSTAL-SMD-2.0X1.2

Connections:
3.3V: 3V3.P$1 (PIN0), 3V3.P$2 (PIN1), 3V3.P$3 (PIN2), C1.1, C2.1, C3.2, C16.1, C19.1, IC1.17 (VDDIO1), IC1.36 (VDDIO2), IC1.44 (VDDIN), JP4.1, L2.1, LED1.A, Q1.1 (G), Q3.1 (G), Q4.1 (G), Q5.1 (G), R1.2, R3.2, R4.2, R7.2, R8.2, R20.2, U1.P$5 (VOUT), U$4.11 (VDD), U$4.12 (VDD3V)
A: U$4.6 (A)
ARDUINO_A0: IC1.3 (PA2/EIC/AIN0), J2.P$9 (PIN8)
ARDUINO_A1: IC1.7 (PB8/EIC/AIN2/SCOM4PAD0/TC4), J2.P$8 (PIN7)
ARDUINO_A2----HEADER_SS: IC1.8 (PB9/EIC/AIN3/SCOM4PAD1//TC4), U$4.1 (CSN)
ARDUINO_A3: IC1.9 (PA4/EIC/REF/AIN4/SCOM0PAD0/TC0), J2.P$7 (PIN6)
ARDUINO_A4: IC1.10 (PA5/EIC/AIN5/SCOM0PAD1/TC0), J2.P$6 (PIN5)
ARDUINO_A5: IC1.47 (PB2/EIC/AIN10/SCOM5PAD0), J2.P$5 (PIN4)
ARDUINO_AREF: C4.1, IC1.4 (PA3/EIC/REF/AIN1), J2.P$10 (PIN9)
ARDUINO_D0: IC1.16 (PA11/EIC/AIN19/SCOM2PAD3+/TC1), Q4.2 (S), R3.1
ARDUINO_D1: IC1.15 (PA10/EIC/AIN18/SCOM2PAD2+/TC1), Q3.2 (S), R20.1
ARDUINO_D2: IC1.23 (PA14/XIN/EIC/SCOM2PAD2+/TC3), Q5.2 (S), R4.1
ARDUINO_D3: IC1.14 (PA9/I2C/EIC/AIN17/SCOM2PAD1+/TC0), Q1.2 (S), R1.1
ARDUINO_D4----VREF2: IC1.13 (PA8/I2C/AIN16/SCOM2PAD0+/TC0), R15.1
ARDUINO_D5----IN3: IC1.24 (PA15/XOUT/EIC/SCOM2PAD3+/TC3), U$1.3 (IN3)
ARDUINO_D6----IN4: IC1.29 (PA20/EIC/SCOM5PAD2+), U$1.4 (IN4)
ARDUINO_D7----IN2: IC1.30 (PA21/EIC/SCOM5PAD3+), U$1.5 (IN2)
ARDUINO_D8----IN1: IC1.11 (PA6/EIC/AIN6/SCOM0PAD2/TC1), U$1.6 (IN1)
ARDUINO_D9----VREF1: IC1.12 (PA7/EIC/AIN7/SCOM0PAD3/TC1), R14.1
ARDUINO_D10_SS: IC1.27 (PA18/EIC/SCOM1PAD2+/TC3), J3.P$1 (PIN0)
ARDUINO_D11_MOSI: IC1.25 (PA16/I2C/EIC/SCOM1PAD0+/TC2), J3.P$2 (PIN1)
ARDUINO_D12_MISO: IC1.28 (PA19/EIC/SCOM1PAD3+/TC3), J3.P$3 (PIN2)
ARDUINO_D13_SCK: IC1.26 (PA17/I2C/EIC/SCOM1PAD1+/TC2), J3.P$4 (PIN3), Q2.1 (G), R16.2
ARDUINO_D20_SDA: IC1.31 (PA22/I2C/EIC/SCOM5PAD0+/TC4), J3.P$5 (PIN4), R8.1
ARDUINO_D21_SCL: IC1.32 (PA23/I2C/EIC/SCOM5PAD1+/TC4), J3.P$6 (PIN5), R7.1
B: U$4.7 (B)
DGI_GPIO0: IC1.22 (PA13/I2C/EIC/SCOM2PAD1+/TC2)
GND: C1.2, C2.2, C3.1, C4.2, C5.2, C7.1, C8.1, C9.2, C11.2, C16.2, C19.2, GND.P$1 (PIN0), GND.P$2 (PIN1), GND.P$3 (PIN2), IC1.5 (GNDANA), IC1.18 (GND1), IC1.35 (GND2), IC1.42 (GND3), J1.5 (GND), JP4.3, JP4.5, JP4.9, L1.2, Q2.2 (S), R16.1, SH1.2, SW2.P$3, SW2.P$4, U1.P$2 (GND/ADJ), U$4.5 (TEST), U$4.13 (GND)
GND2: C6.2, C12.-, C13.2, C14.2, C15.2, MOTOR_POWER.2, R12.2, R13.2, SH1.1, U$1.1 (GND), U$1.8 (GND2), U$1.P$1 (GND)
HEADER_MISO: IC1.21 (PA12/I2C/EIC/SCOM2PAD0+/TC2), U$4.3 (MISO)
HEADER_MOSI: IC1.19 (PB10/EIC/SCOM4PAD2/TC5), U$4.4 (MOSI)
HEADER_SCK: IC1.20 (PB11/EIC/SCOM4PAD3/TC5), U$4.2 (CLK)
HV1: J2.P$3 (PIN2), Q3.3 (D), R21.1
HV2: J2.P$4 (PIN3), Q4.3 (D), R2.1
HV3: J2.P$2 (PIN1), Q5.3 (D), R11.1
HV4: J2.P$1 (PIN0), Q1.3 (D), R6.1
I: U$4.14 (I)
unnamed: LED1.C, R5.2
unnamed: R12.1, U$1.14 (LSS34)
unnamed: Q2.3 (D), R5.1
unnamed: R13.1, U$1.11 (LSS12)
unnamed: C15.1, R15.2, U$1.2 (VREF34)
unnamed: JP6.4, U$1.15 (OUT4)
unnamed: JP6.1, U$1.10 (OUT1)
unnamed: JP6.2, U$1.12 (OUT2)
unnamed: JP6.3, U$1.13 (OUT3)
unnamed: C14.1, R14.2, U$1.7 (VREF12)
unnamed: D1.ANODE, F1.2
unnamed: F1.1, J1.1 (5V)
PA00_XIN32: C7.2, IC1.1 (PA0/XIN32/EIC/SCOM1PAD0/TC2), Y1.2
PA01_XOUT32: C8.2, IC1.2 (PA1/XOUT32/EIC/SCOM1PAD1/TC2), Y1.1
PA27_TX_LED: IC1.39 (PA27/EIC)
PA28_USB_HOST_EN: IC1.41 (PA28/EIC)
PA30_SWCLK: IC1.45 (PA30/EIC/SCOM1PAD2/TC1), JP4.4
PA31_SWDIO: IC1.46 (PA31/EIC/SCOM1PAD3/TC1), JP4.2
PB03_RX_LED: IC1.48 (PB3/EIC/AIN11/SCOM5PAD1)
RESET: IC1.40 (RESETN), JP4.10, SW2.P$1, SW2.P$2
RXD: IC1.38 (PB23/EIC/SCOM5PAD3)
SHIELD: J1.S1 (SLD), J1.S2 (SLD), J1.S3 (SLD), J1.S4 (SLD), J1.S5 (SLD), J1.S6 (SLD), J1.S7 (SLD), J1.S8 (SLD), L1.1
TARGET_USB_N: IC1.33 (PA24/EIC/SCOM3PAD2+/TC5), J1.2 (D-)
TARGET_USB_P: IC1.34 (PA25/EIC/SCOM3PAD3+/TC5), J1.3 (D+)
TXD: IC1.37 (PB22/EIC/SCOM5PAD2)
V+: C6.1, C12.+, C13.1, MOTOR_POWER.1, U$1.9 (VBB), U$1.16 (VBB2), V+.P$1 (PIN0), V+.P$2 (PIN1), V+.P$3 (PIN2)
VDDANA: C5.1, IC1.6 (VDDANA), L2.2
VDDCORE: C11.1, IC1.43 (VDDCORE1)
VIN: C9.1, D1.CATHODE, R2.2, R6.2, R11.2, R21.2, U1.P$1 (VIN), U1.P$3 (EN), VIN.P$1 (PIN0), VIN.P$2 (PIN1), VIN.P$3 (PIN2)

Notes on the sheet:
A0 = DAC
All analog pins can be used as digital pins.
LED draws 4mA.
A2 is SS for SPI header.
Use VOUT or the 3V3 pins to power external modules.
Ferrite bead prevents USB cable sheild from acting like an antenna.
3.3V linear regulator
Magnetic Encoder
SAMD21
PWM Motor Driver
VIN: 5V (3.3V is ok if USB is not plugged in.)
TLV70233PDBVR ---------------- Iout (max): 300mA Vin (max): 6.0V Vdo (typ): 220mV Iq: 35uA
A4954
Micro USB
Joe Church
Based on: Arduino Zero by Arduino.cc Arduino M0 by Arduino.org Neutrino by Rabidprototypes.com SAMD21 Dev Breakout by Sparkfun.com
0.1
Arduino Zero Compatible
Mechaduino

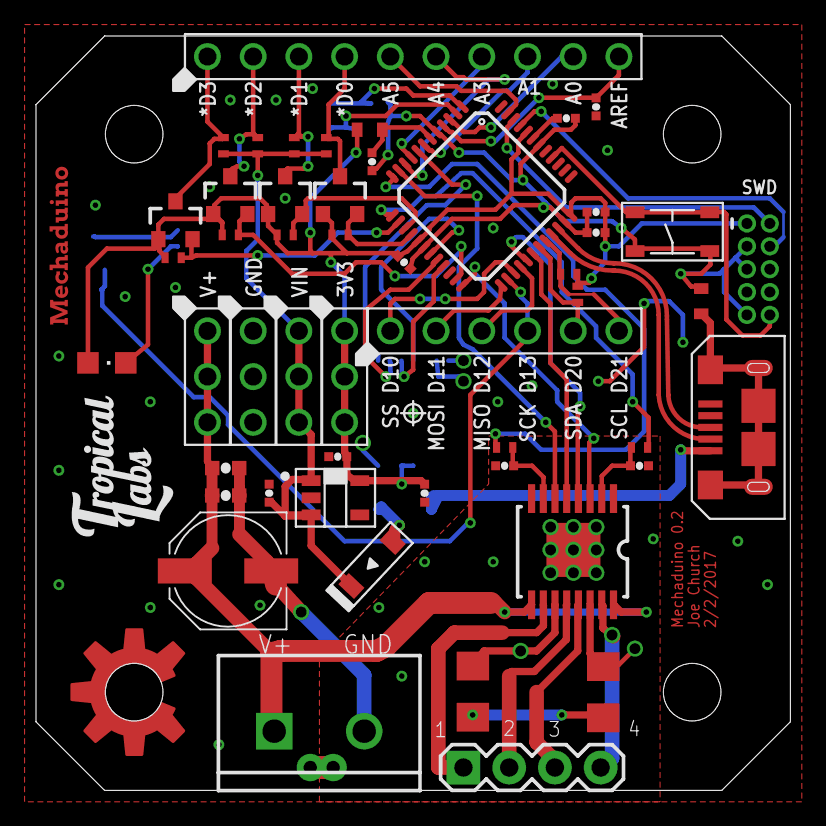
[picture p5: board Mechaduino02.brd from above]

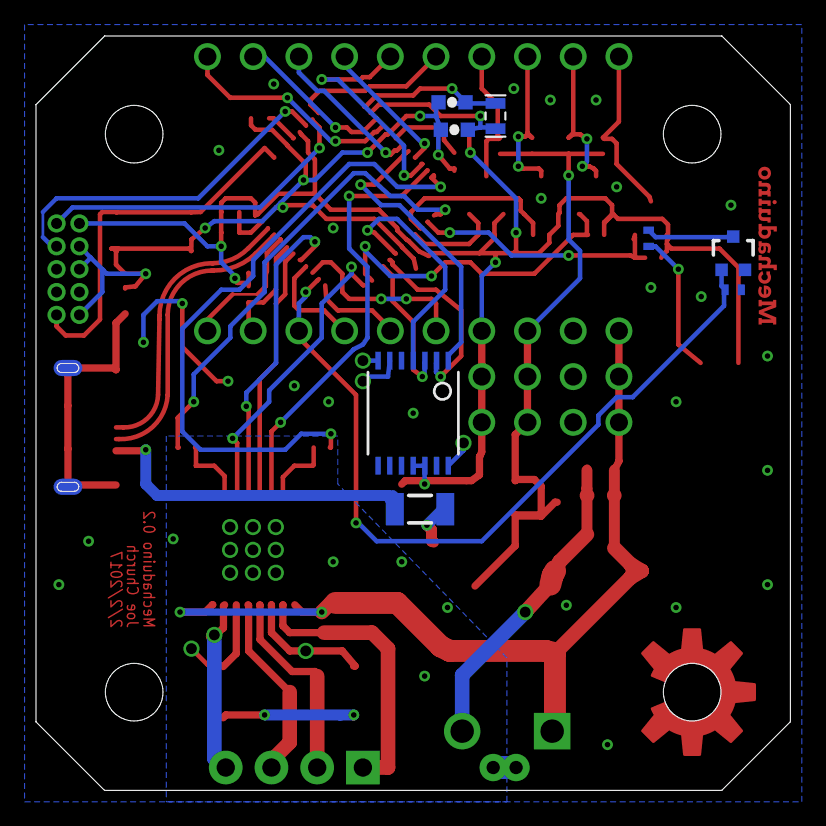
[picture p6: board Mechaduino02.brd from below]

Board: 2 copper layers, 41.9 x 41.9 mm, 64 parts (8 on the bottom side), 57 nets.

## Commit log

2016-03-24 copied from v 0.0
    baseline
    [Mechaduino01.brd, Mechaduino01.sch]
2016-03-26 cleaned up
    including net labels
    [Mechaduino01.brd]
2016-03-26 Updated power supply
    Borrowed from sparkfun samd21 pro
2016-03-26 hardwired encoder, driver
    [Mechaduino01.brd, Mechaduino01.sch]
2016-03-26 formatted and added license
    [Mechaduino01.brd, Mechaduino01.sch]
2016-03-27 ready for layout
    ripped up old stuff, shrunk to 1.65" square from 1.7" and moved
    placement sensitive parts accordingly
    [Mechaduino01.brd, Mechaduino01.sch]
2016-03-27 added level shifter
    on D0, D1
    [Mechaduino01.brd, Mechaduino01.sch]
2016-03-31 cut corners
    [Mechaduino01.brd]
2016-03-31 cut corners...
    resaved
    [Mechaduino01.brd]
2016-04-02 replaced through hole passives with smd
    [Mechaduino01.brd, Mechaduino01.sch]
2016-04-09 fixed last unrouted
    also increased polygon isolate to 8 thou
    [Mechaduino01.brd]
2016-04-12 reviewed
    updated graphics, checked stuff... done?
    [Mechaduino01.GBL, Mechaduino01.GBO, Mechaduino01.GBP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]
2016-04-19 Final
    ordered
    [Mechaduino01.GBL, Mechaduino01.GBO, Mechaduino01.GBP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]
2016-06-03 Made CSV openable via excel
    [Mechaduino01.csv]
2016-06-04 Zipped Gerber Files :paperclip:
    [Mechaduino01.GBL, Mechaduino01.GBO, Mechaduino01.GBP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]
2016-06-04 Moved and Renamed BOM Files :page_with_curl:
    [Mechaduino01_BOM.csv]
2016-06-24 Current sense
    changed Rsense from 0.25 ohm to 0.15 ohm
2016-08-09 Fix case sensitivity on 100k res
    Case sensitivity in BOM export causes 2 seperate entries in the BOM
    under the 100k resistors. Ks are mostly capitalized throughout the
    schematic, so corrected this one.
    [Mechaduino01.sch]
2016-08-09 100k to 100K
    [Mechaduino01.brd]
2016-08-11 changed BOM C10,C18
    from 0402 to 0805 (matched board now)
    [Mechaduino01_BOM.csv]
2016-08-14 Fixed AP2112K-3.3
    [Mechaduino01_BOM.csv]
2016-08-24 Gerbers updated
    [Mechaduino01.GBL, Mechaduino01.GBO, Mechaduino01.GBS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]
2016-08-24 updated Gerber .zip
2016-09-26 Updated rSense
    [Mechaduino01_BOM.csv]
2017-01-27 minor change to as5047 power circuit
    [Mechaduino01.brd, Mechaduino01.sch]
2017-01-27 added third level shifter (same as others)
    [Mechaduino01.brd, Mechaduino01.sch]
2017-01-29 fixed thermal and a4954 clearance
    [Mechaduino01.brd]
2017-02-01 moved IO headers down 0.01
    [Mechaduino01.brd, Mechaduino01.sch]
2017-02-01 moved things around
    [Mechaduino01.brd, Mechaduino01.sch]
2017-02-03 commit after rollback issues
    [Mechaduino01.brd, Mechaduino01.sch]
2017-02-03 almost completely routed
    [Mechaduino01.brd]
2017-02-03 passes DRC
    should still double check
    [Mechaduino01.brd]
2017-02-03 minor fixes
    [Mechaduino01.brd]
2017-02-03 moved button
    [Mechaduino01.brd]
2017-02-03 updated caps
    [Mechaduino01.brd, Mechaduino01.sch]
2017-02-03 reday to order
    [Mechaduino01.brd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]
2017-02-03 fixed file names, also silkscreen for *D3,*D2
    [Mechaduino02.GBL, Mechaduino02.GBO, Mechaduino02.GBS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]
2017-02-03 fixed bom
    [Mechaduino02.csv]
2017-02-03 via stitching
    cleaned up ground pours
    [Mechaduino02.brd, Mechaduino02.sch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]
2017-02-03 fixed xtal caps and power caps to 0603
    [Mechaduino02.brd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]
2017-02-03 moved vias away from header
    [Mechaduino02.brd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]
2017-03-19 a couple more changes
    fixed cap sizes? changed some text under regulator
    [Mechaduino02.sch]
2017-04-28 fixed BOM, header
    [Mechaduino01_BOM.csv, Mechaduino02_BOM.csv]
2017-04-28 removed 0.1 files
    [Mechaduino01.GBL, Mechaduino01.GBO, Mechaduino01.GBS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]
2017-05-04 updated schematic text
    [Mechaduino02.sch]
2017-05-04 re-exported image, libraries
    [Mechaduino02.brd, Mechaduino02.sch]
2017-05-04 updated image
    [Mechaduino02.sch]

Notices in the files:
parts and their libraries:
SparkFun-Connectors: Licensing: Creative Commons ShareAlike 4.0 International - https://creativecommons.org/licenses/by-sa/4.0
